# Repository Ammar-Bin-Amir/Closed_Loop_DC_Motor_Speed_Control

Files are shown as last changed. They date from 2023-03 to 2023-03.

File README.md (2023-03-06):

# Closed Loop DC Motor Speed Control

A speed control system's goal is to keep the motor's speed constant under a variety of circumstances. The DC motor is a nonlinear device in practice and speed variations are caused by disturbances, changes in load demand, etc. In this projet, the PID controller algorithm, a common controller in industries, has been implemented which overcome the disturbances occurring in the system and establishes the motor speed to the desired value without any human assistance.

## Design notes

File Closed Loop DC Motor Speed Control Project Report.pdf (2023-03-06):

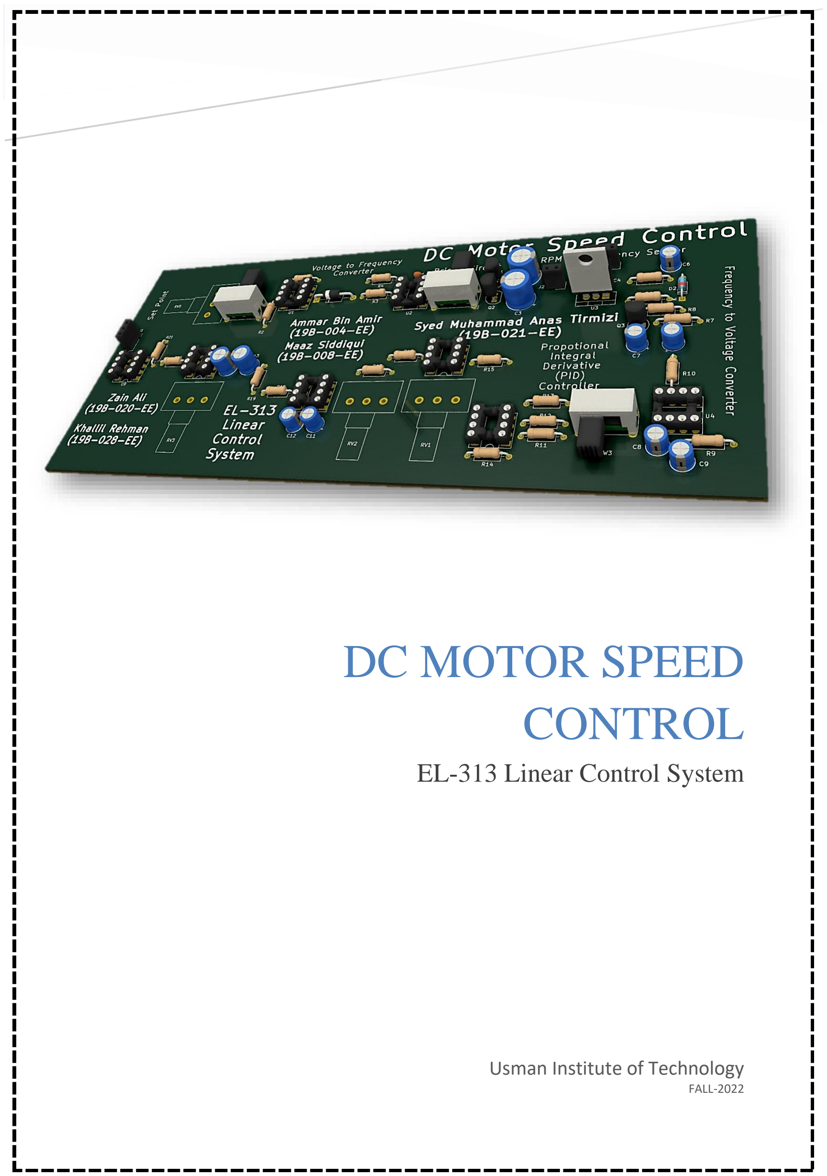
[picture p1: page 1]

# DC MOTOR SPEED CONTROL

## EL-313 Linear Control System

### Usman Institute of Technology

FALL-2022

### Table of Contents

I. Abstract | 2
II. Introduction | 2
III. Literature Review | 3
A. DC Motor Specifications | 3
i. Field Control | 3
ii. Armature Control | 3
B. PID Controller | 3
IV. Proposed System Description | 4
V. Important Observations | 4
VI. | Schematic | 5
VII. | Simulation | 5
VIII. | Hardware | 7
IX. | Tentative Output | 8
X. Problem Faced and Solution | 9
I. Testing Results | 9
II. Conclusion and Future Work | 9
III. References | 9

Table of Tables
Table 1: Parameters of PID Controller | 4

Table of Figures
Figure 1: Block Diagram of DC Motor Speed Control | 2
Figure 2: Block Diagram of PID Controller | 3
Figure 3: Schematic of DC Motor Speed Control | 5
Figure 4: Circuit of PID Controller | 5
Figure 5: Waveforms of PID Controller | 6
Figure 6: Circuit of Voltage to Frequency Converter | 6
Figure 7: Waveforms of Voltage to Frequency Converter | 6
Figure 8: Circuit of Frequency to Voltage Converter | 6
Figure 9: Waveforms of Frequency to Voltage Converter | 6
Figure 10: Circuit of DC Motor Speed Control | 7
Figure 11: Waveforms of DC Motor Speed Control | 7
Figure 12: 2D Layout of PCB | 8
Figure 13: Front 3D Layout of DC Motor Speed Control | 8
Figure 14: Back 3D Layout of DC Motor Speed Control | 8
Figure 15: Front Silk Screen Layer of PCB | 8

I. Abstract

The function of speed control in DC motors is very essential in the achievement of desirable outputs. DC motors are designed for use in industrial and commercial applications. Proportional-Integral-Derivative (PID) controller are considered for controlling the speed of dc motor by giving the step input signal. The response of the motor is investigated using a first order system model of the motor.

An implementation of the controller utilizing OP-AMPs is provided, along with an explanation of the speed control using PID control modes. Designers examine how the controller reacts to changes in load. The system is simulated using KICAD/SIMULINK software. The system responses under PID controllers are also analyzed and discussed in term of their performances.

II. Introduction

It was mainly about P, P-I, P-D and P-I-D controllers, their digital versus continuous time realizations and their characteristics including sampling period effects on the response of digital ones.

A speed control system's goal is to keep the motor's speed constant under a variety of circumstances. The DC motor is a nonlinear device in practice, and speed variations are caused by disturbances, changes in load demand, etc.

The PID controller algorithm, a common controller in industries, has been implemented. The block diagram of a DC motor speed control system. The motor speed is sensed by an optical switch and converted to feedback voltage. It is compared with the reference signal (i.e., desired speed) by the error detector. The PID controller acts on the error signal and generates appropriate control voltage. The PWM generator block than varies the duty cycle of the voltage supplied to the motor to control its speed.

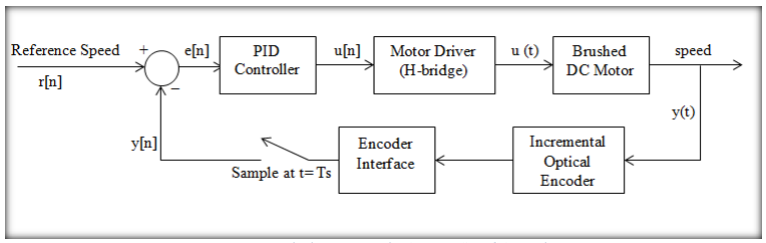
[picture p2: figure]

Figure 1: Block Diagram of DC Motor Speed Control

III. Literature Review

For the implementation of the DC motor speed control system, the concepts of motor and PID controller should be understood.

A. DC Motor Specifications

The speed control system was implemented for a Permanent Magnet DC Motor (PMDC). The PMDC consists of rotor or armature and a stator, which is a permanent magnet. There are two ways of speed control for a DC motor.

i. Field Control

In this method, the field current or current through stator is varied to control the speed of the motor.

ii. Armature Control

In this method, the armature voltage is varied to control the speed of the motor.

For the PMDC, a constant field is generated by a permanent magnet and hence we decided to implement Armature control. To control the armature voltage, we are generating a Pulse-Width Modulated (PWM) waveform to control the average voltage applied to the motor.

B. PID Controller

The combination of proportional, integral and derivative control action is called PID control action. PID controllers are commonly used to regulate the time-domain behavior of many different types of dynamic plants. These controllers are extremely popular because they can usually provide good closed-loop response characteristics.

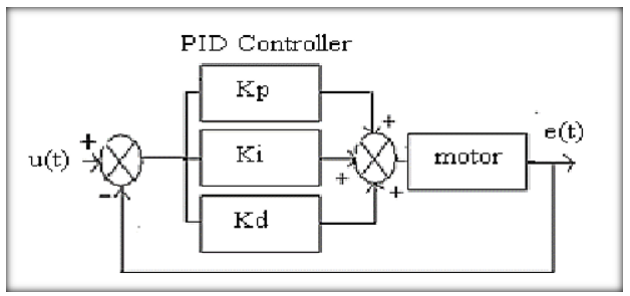
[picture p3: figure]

Figure 2: Block Diagram of PID Controller

Table 1: Parameters of PID Controller

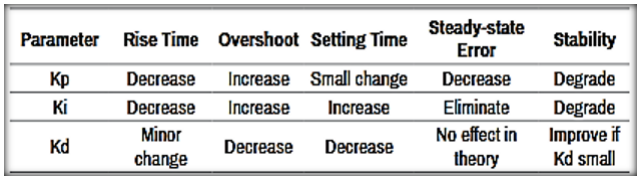
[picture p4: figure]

IV. Proposed System Description

The actual speed of the motor is sensed by the feedback control loop and compares this speed with the preset reference speed in order to determine the required motor’s reference armature current. The simulation of proposed system model has been accomplished.

The PID controller is very popular and common in process control industry. In the PID (proportional-integral-derivative) closed control loop controller, the three controllers P, I and D all have different tuning adjustments which interact all together that’s why its tuning is time consuming and challenging task. The effects of all three individual controllers (P-I-D) summed together to produce the output value of the system. Tuning of PID controller is the major task of this device in order to proper functioning of the PID controller under the given circumstance of the control system.

The variable stand for the error signal used to track the reference signal. The variable is the difference between the desired reference input set point value and the actual output. This error signal is sent to the PID controller and then controller evaluates the derivative and the integral of the error signal. The output signal of the controller becomes equal to the proportional gain (KP) times the magnitude of the error plus the integral gain (KI) times the integral of the error plus the derivative gain (KD) times the derivative of the error.

V. Important Observations

Accurate performance of a motor is desired feature for any industrial application. As the age of motor increases its performance also deceases with aging, so it is desired to evaluate the performance of motor from time to time for efficient operation The conventional method for calculating output performance indices is quite time consuming.

The PID based approach algorithm worked satisfactory for the test system. Following are the observations:

1) The solution time for proposed PID approach is only a fraction of time taken by
| conventional algorithm.
2) A proportional controller Kp will have the effect of reducing the rise time and reduce
| but never eliminate the steady state error.
3) An internal controller Ki will have the effect of eliminate the steady state error, but it
| may make the transient response worse.

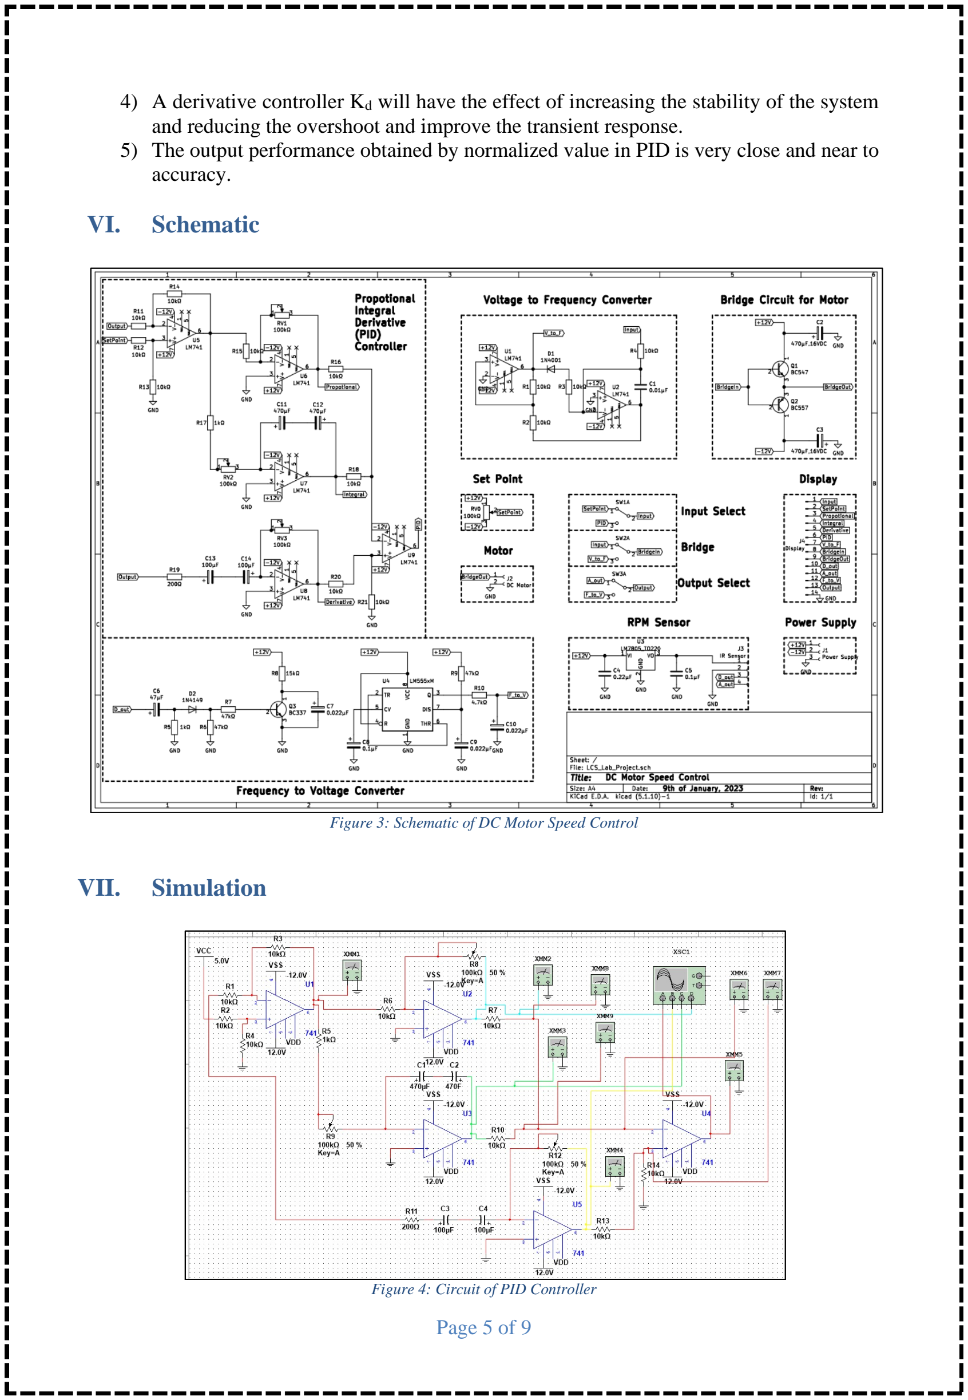
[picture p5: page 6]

4) A derivative controller Kd will have the effect of increasing the stability of the system and reducing the overshoot and improve the transient response.
5) The output performance obtained by normalized value in PID is very close and near to accuracy.

VI. Schematic

Figure 3: Schematic of DC Motor Speed Control

VII. Simulation

Figure 4: Circuit of PID Controller

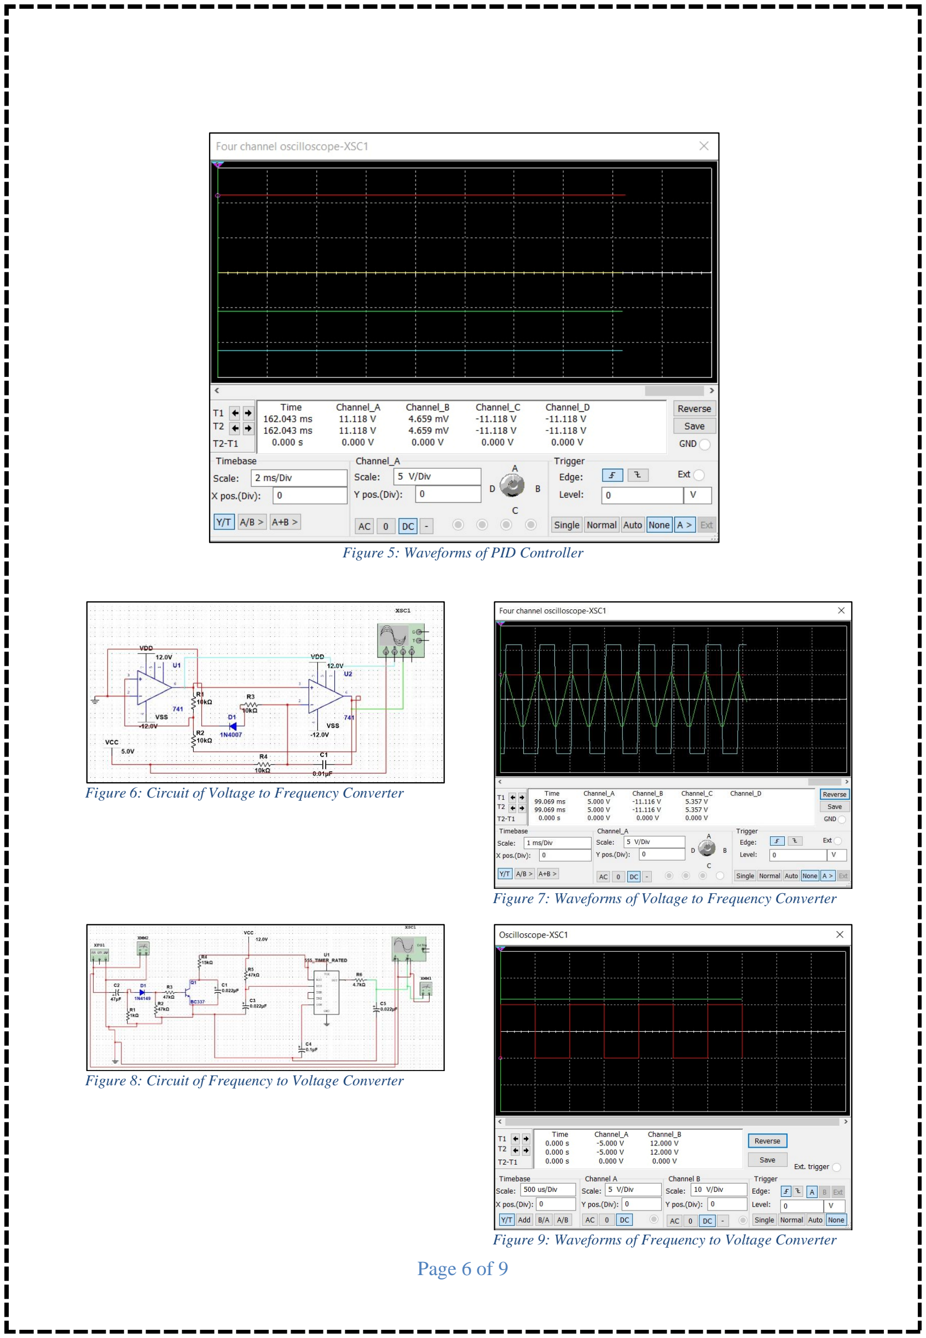
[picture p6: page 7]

Figure 5: Waveforms of PID Controller

Figure 6: Circuit of Voltage to Frequency Converter

Figure 7: Waveforms of Voltage to Frequency Converter

Figure 8: Circuit of Frequency to Voltage Converter

Figure 9: Waveforms of Frequency to Voltage Converter

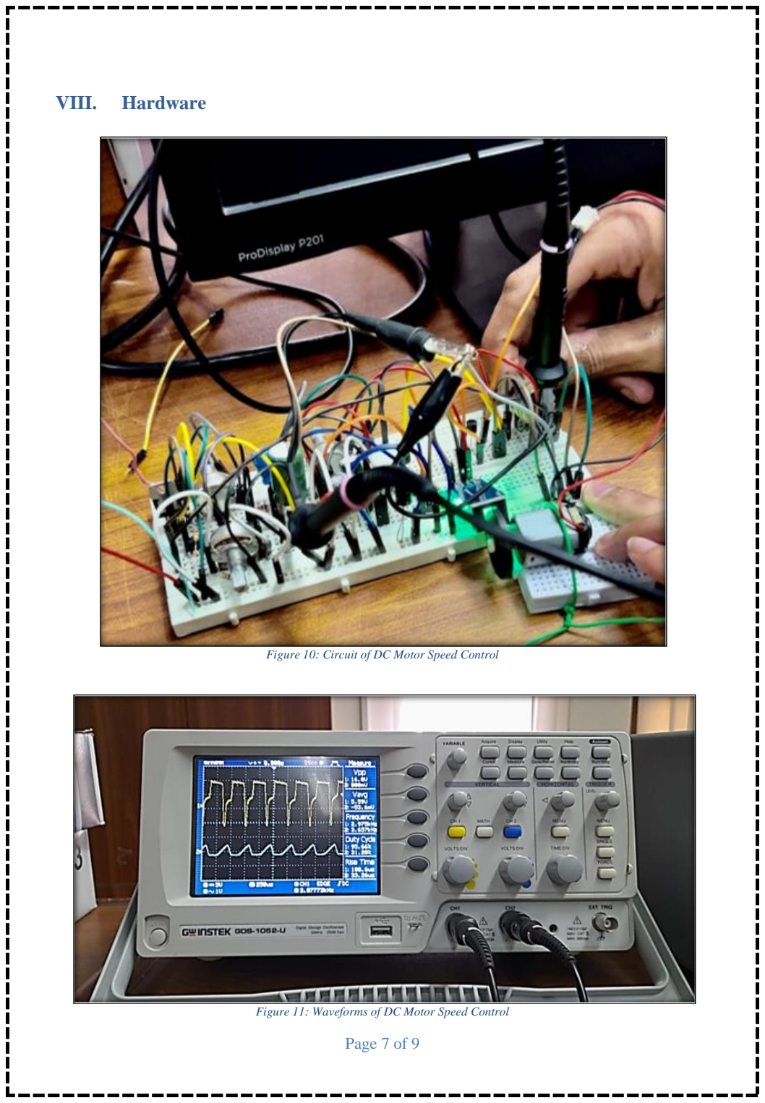
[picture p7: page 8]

VIII. Hardware

Figure 10: Circuit of DC Motor Speed Control

Figure 11: Waveforms of DC Motor Speed Control

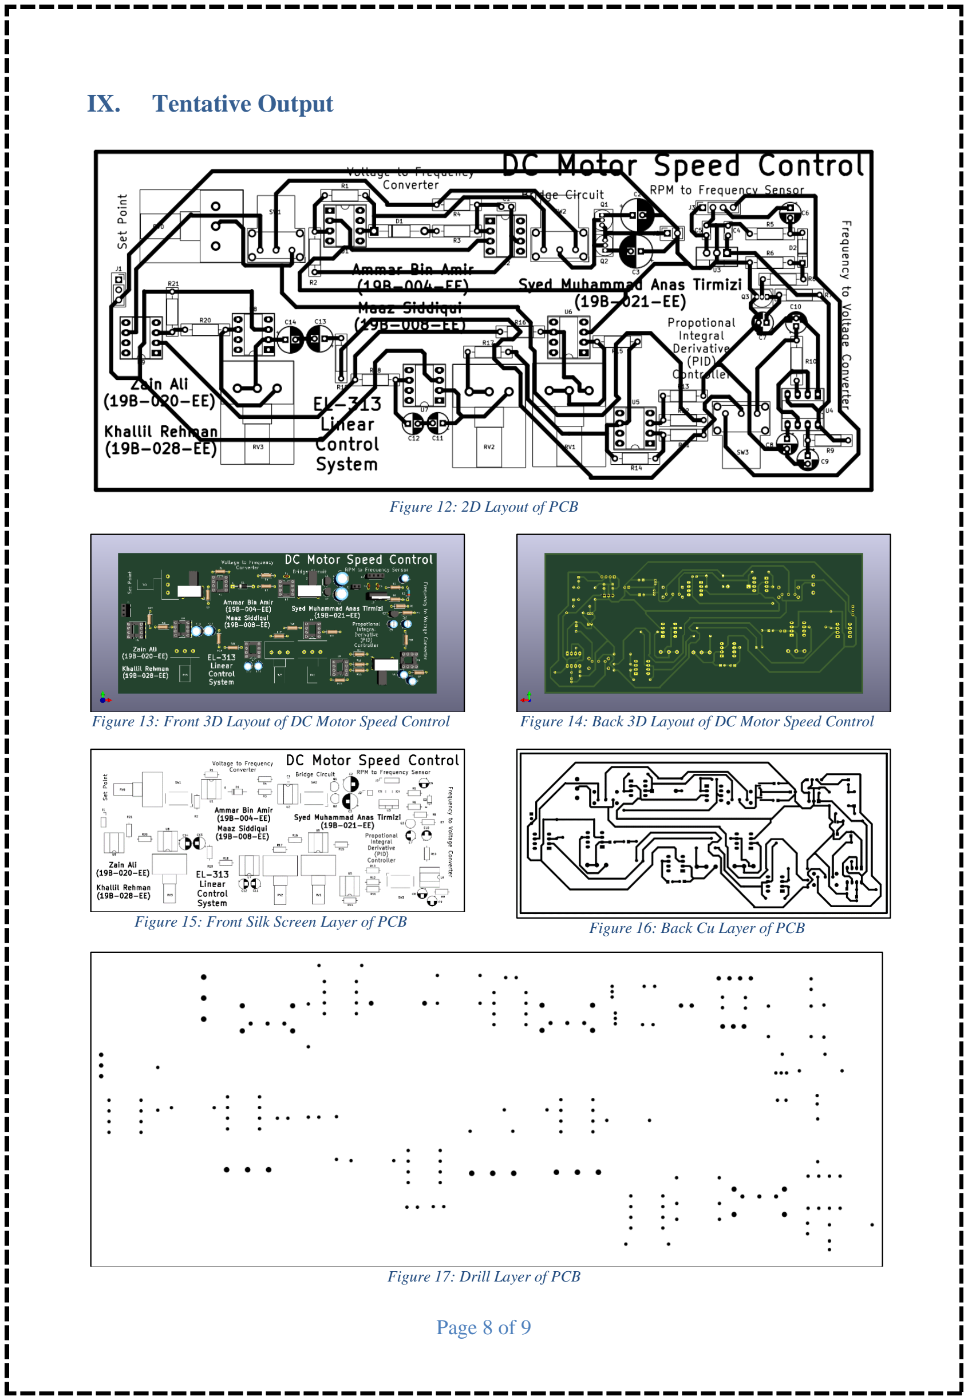
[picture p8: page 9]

IX. Tentative Output

Figure 12: 2D Layout of PCB

Figure 13: Front 3D Layout of DC Motor Speed Control | Figure 14: Back 3D Layout of DC Motor Speed Control
Figure 15: Front Silk Screen Layer of PCB | Figure 16: Back Cu Layer of PCB

Figure 17: Drill Layer of PCB

X. Problem Faced and Solution

To reduce this offset, we modified the circuit to bring back the triangular wave output to the zero reference level. The modified circuit schematic. The circuit uses the feedback mechanism with the comparator (LM 339) and integrator circuit to correct the DC offset error and brings back the triangular wave output to zero reference level. Because of this error correction we are able to generate the PWM pulses from 0% to 100% duty cycle after comparing this triangular wave with the controlled output from PID controller.

I. Testing Results

The DC motor control system was tested with PI and PID controllers. The output waveforms of the PWM generator for two different reference voltage (corresponding to desired speed) and under full load and no-load condition are shown in this section. The DC motor is loaded by magnetic breaking to study the controller performance under load conditions.

II. Conclusion and Future Work

P-I-D control and its variations are commonly used in the industry. They have so many applications. Control engineers usually prefer P-I controllers to control first order plants. On the other hand, P-I-D control is vastly used to control two or higher order plants. In almost all cases fast transient response and zero steady state error is desired for a closed loop system.

However, some improvements can be made in the control aspects of the proposed system design. In this experiment, the PID controller is well performed for the motor speed control under the loaded condition while the speed is kept constant. The ultimate parameter values of PID controller were setup by Manual Tuning method. An Adaptive approach of PID controller may be used in the prospective development in order of effectively speed control of the motor with reference to input speed under the effect of load.

III. References

https://www.elprocus.com/the-working-of-a-pid-controllerhttps://ctms.engin.umich.edu/CTMS/index.php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

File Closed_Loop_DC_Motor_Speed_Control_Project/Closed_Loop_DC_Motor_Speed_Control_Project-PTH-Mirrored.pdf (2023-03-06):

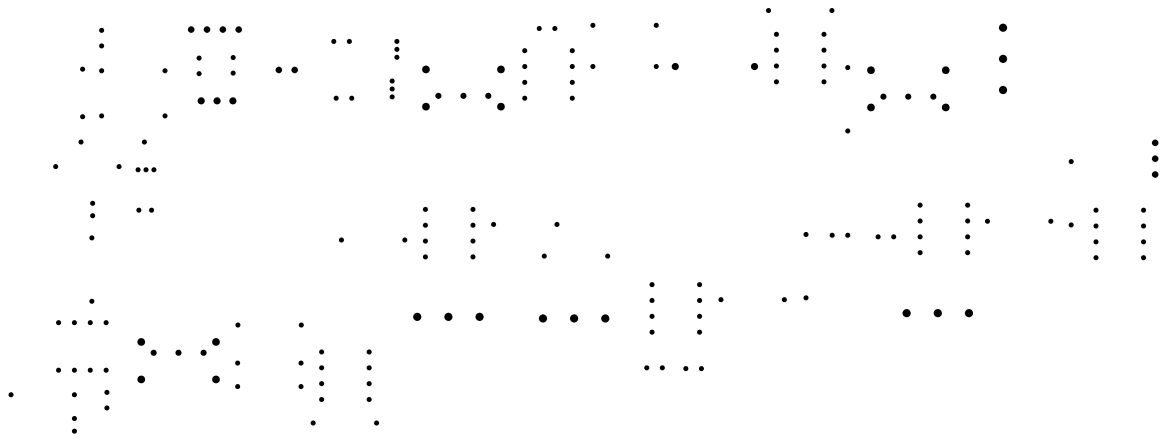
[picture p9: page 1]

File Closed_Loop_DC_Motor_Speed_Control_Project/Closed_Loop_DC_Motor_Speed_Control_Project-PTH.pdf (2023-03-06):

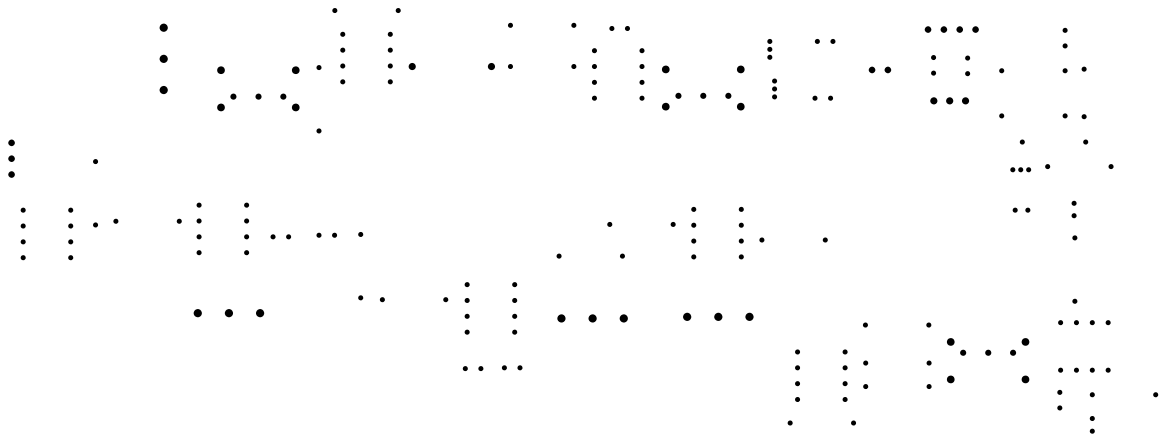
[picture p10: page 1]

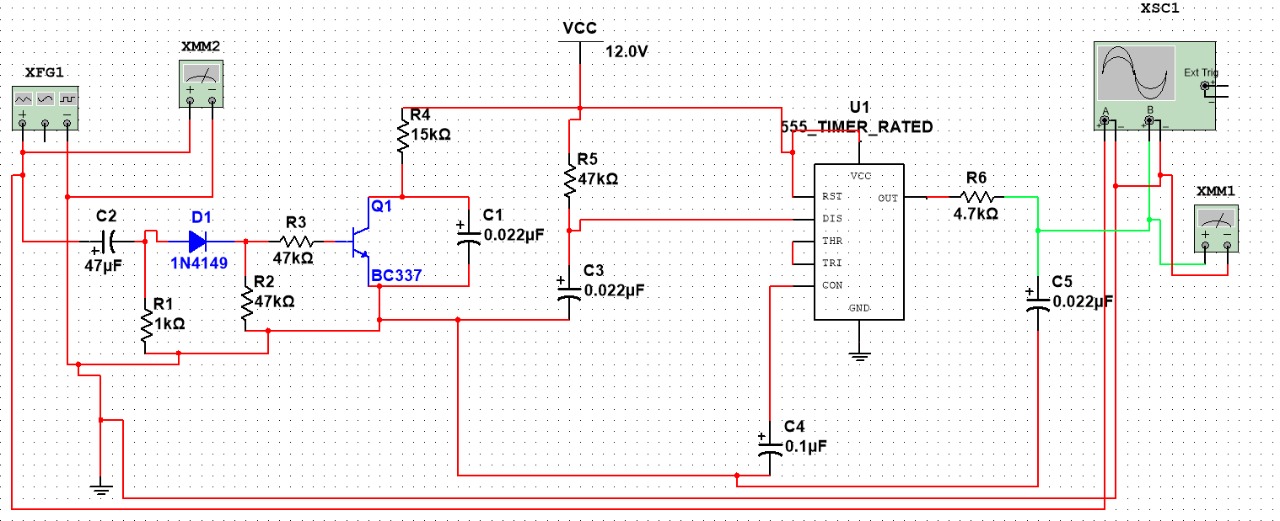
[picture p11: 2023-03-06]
Frequency to Voltage Converter Schematic.jpeg

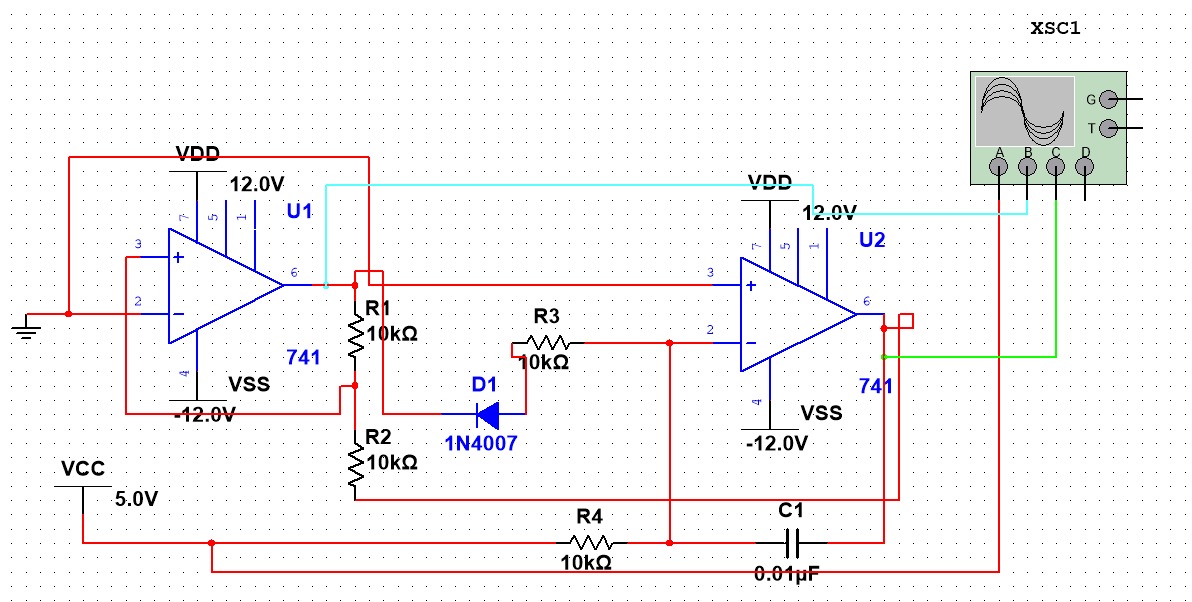
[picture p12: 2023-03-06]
Voltage to Frequency Converter Schematic.jpeg

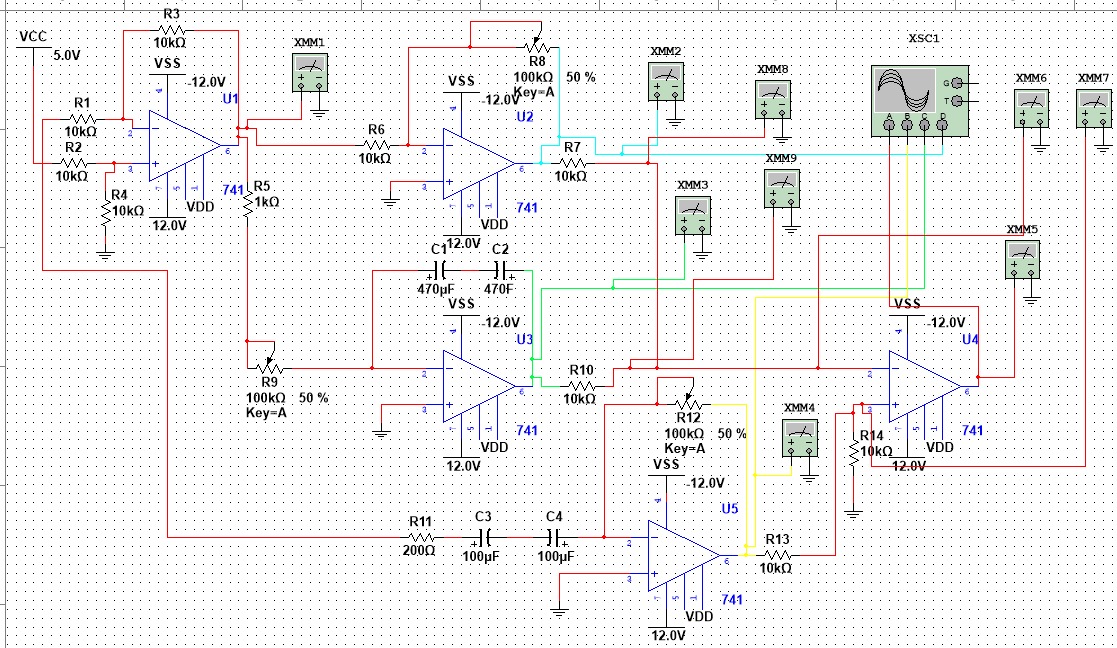
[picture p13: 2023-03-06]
PID Controller Schematic.jpeg

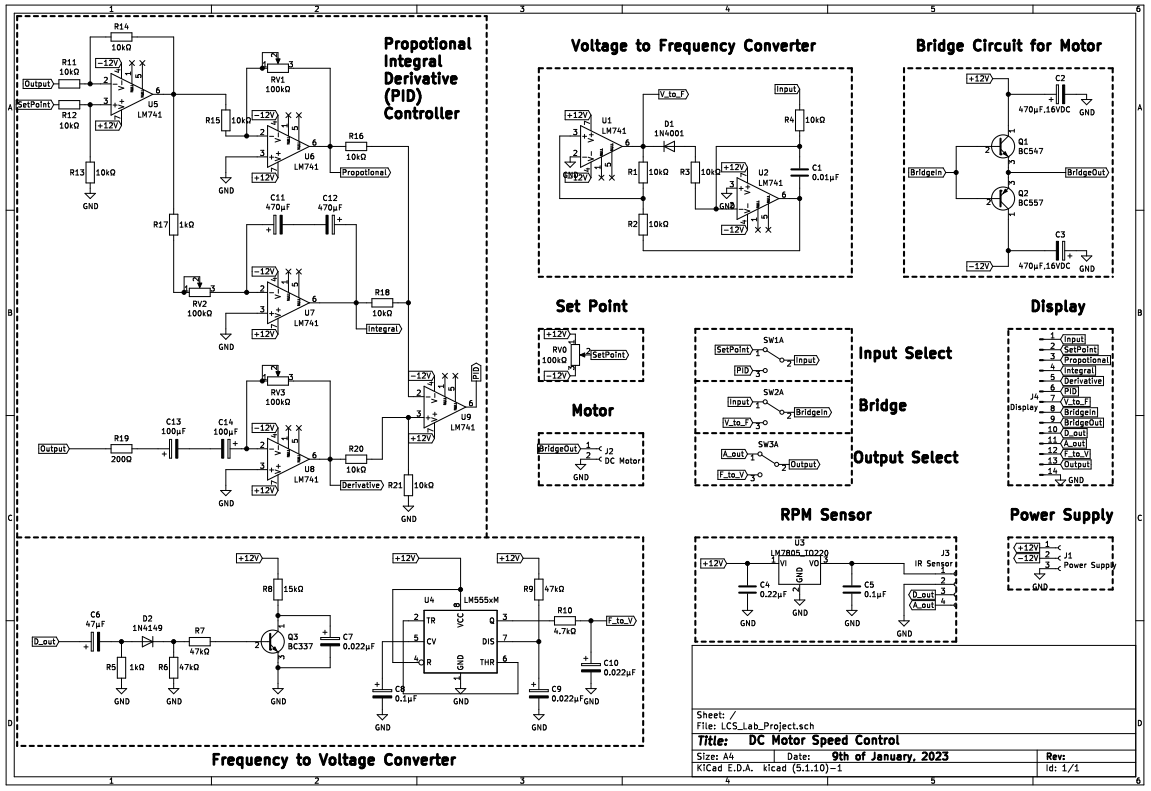
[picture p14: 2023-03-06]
Closed_Loop_DC_Motor_Speed_Control_Project/Closed_Loop_DC_Motor_Speed_Control_Project_Schematic.PNG

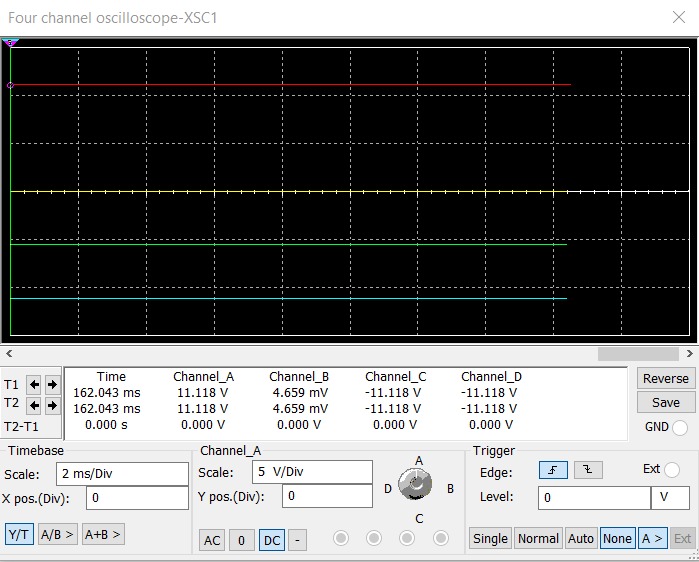
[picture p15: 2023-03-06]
PID Controller Simulation.jpeg

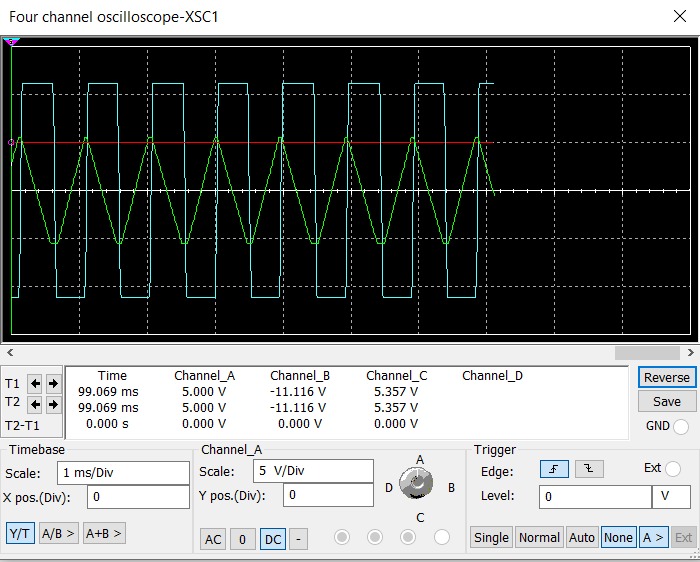
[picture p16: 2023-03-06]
Voltage to Frequency Converter Simulation.jpeg

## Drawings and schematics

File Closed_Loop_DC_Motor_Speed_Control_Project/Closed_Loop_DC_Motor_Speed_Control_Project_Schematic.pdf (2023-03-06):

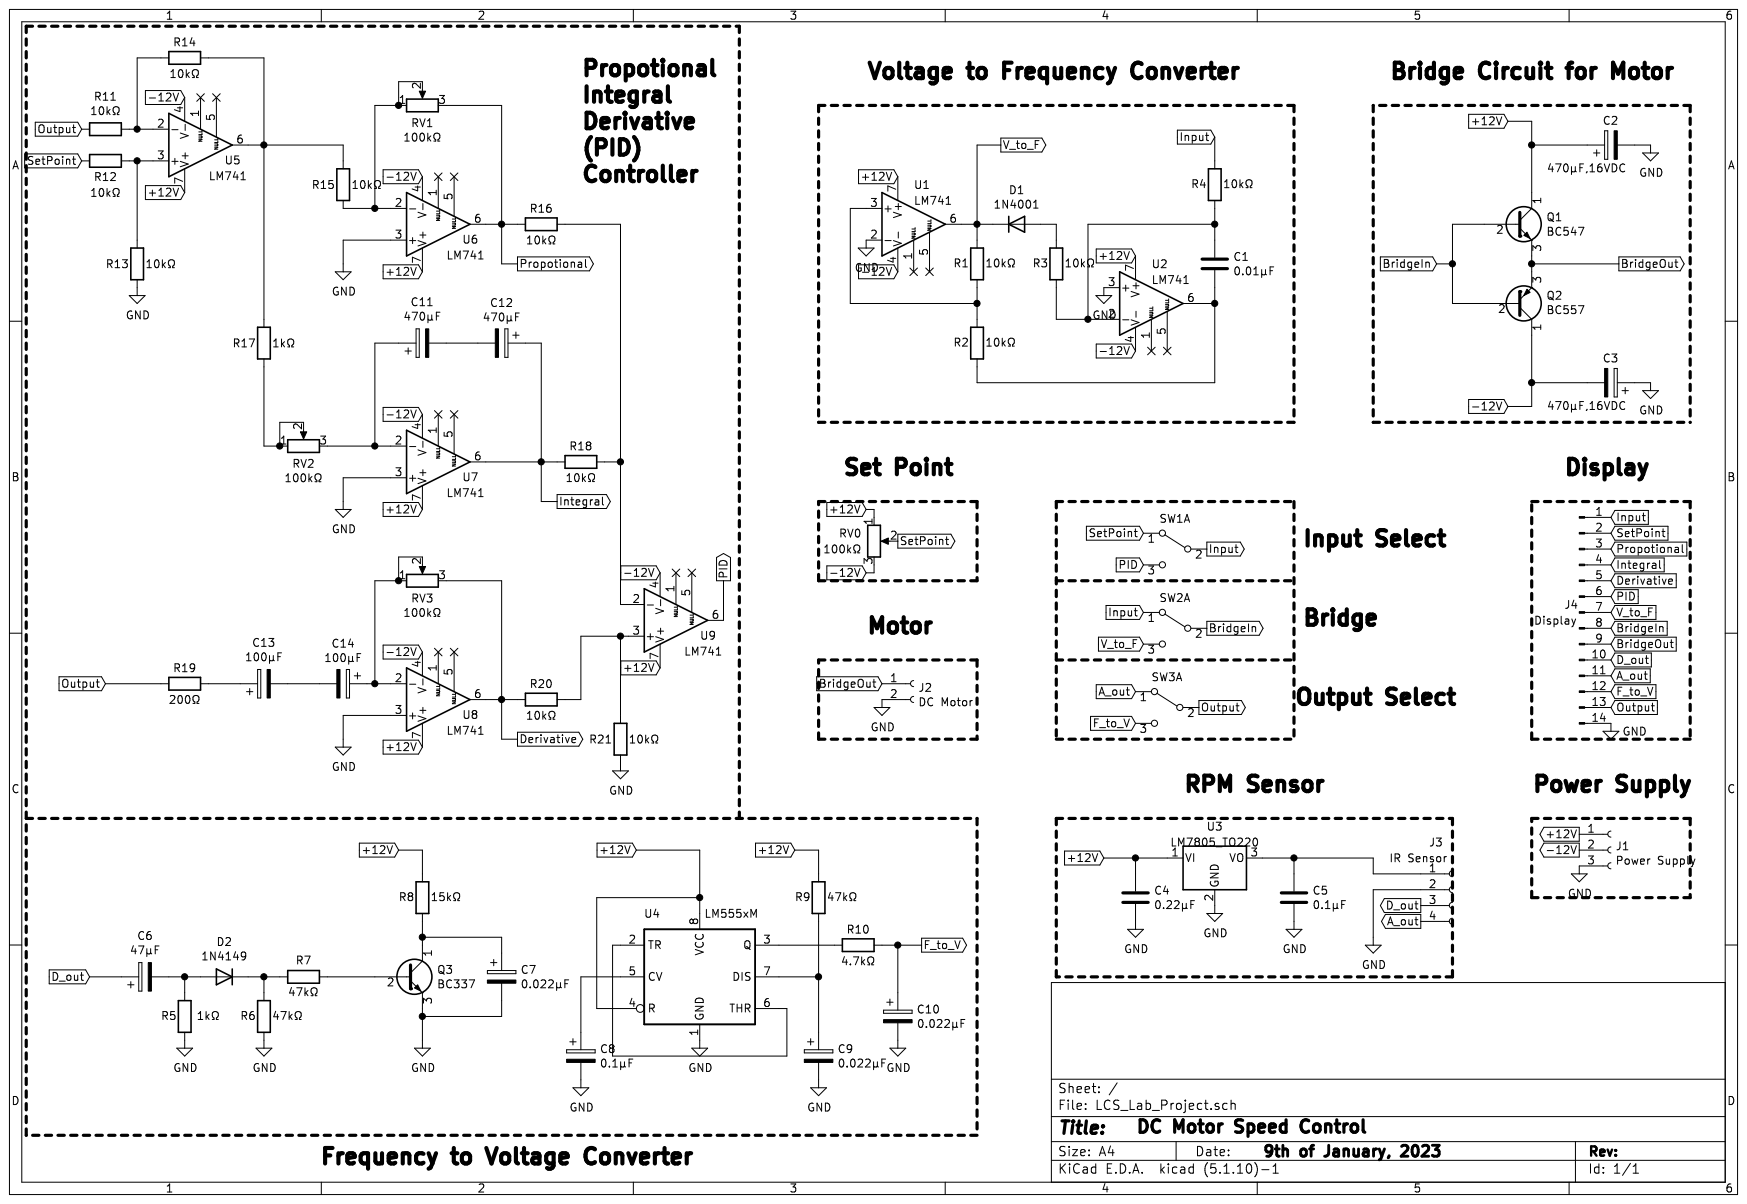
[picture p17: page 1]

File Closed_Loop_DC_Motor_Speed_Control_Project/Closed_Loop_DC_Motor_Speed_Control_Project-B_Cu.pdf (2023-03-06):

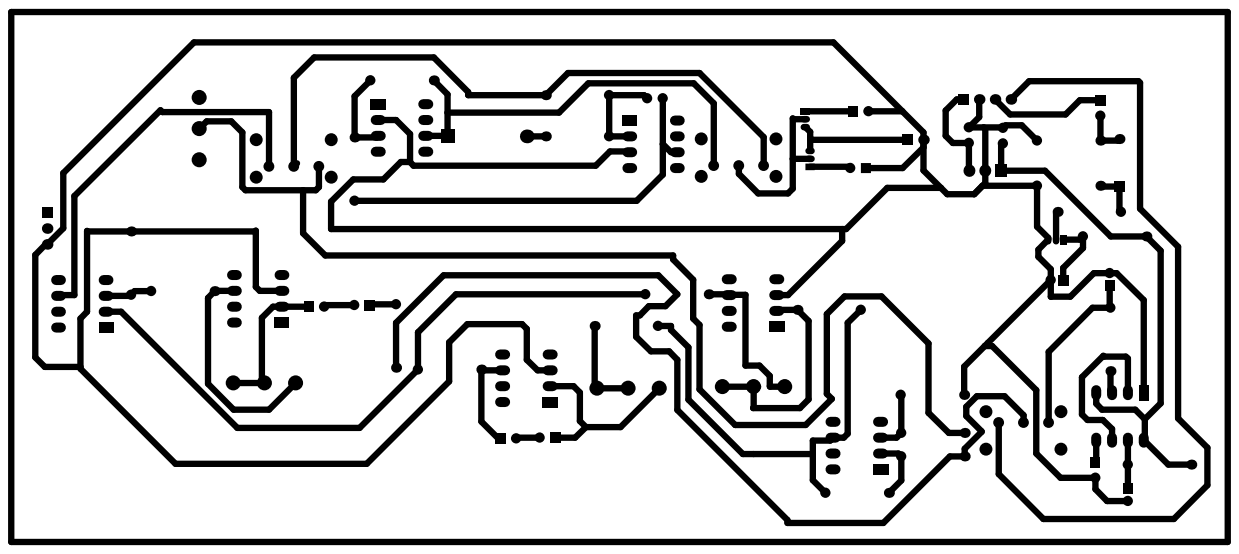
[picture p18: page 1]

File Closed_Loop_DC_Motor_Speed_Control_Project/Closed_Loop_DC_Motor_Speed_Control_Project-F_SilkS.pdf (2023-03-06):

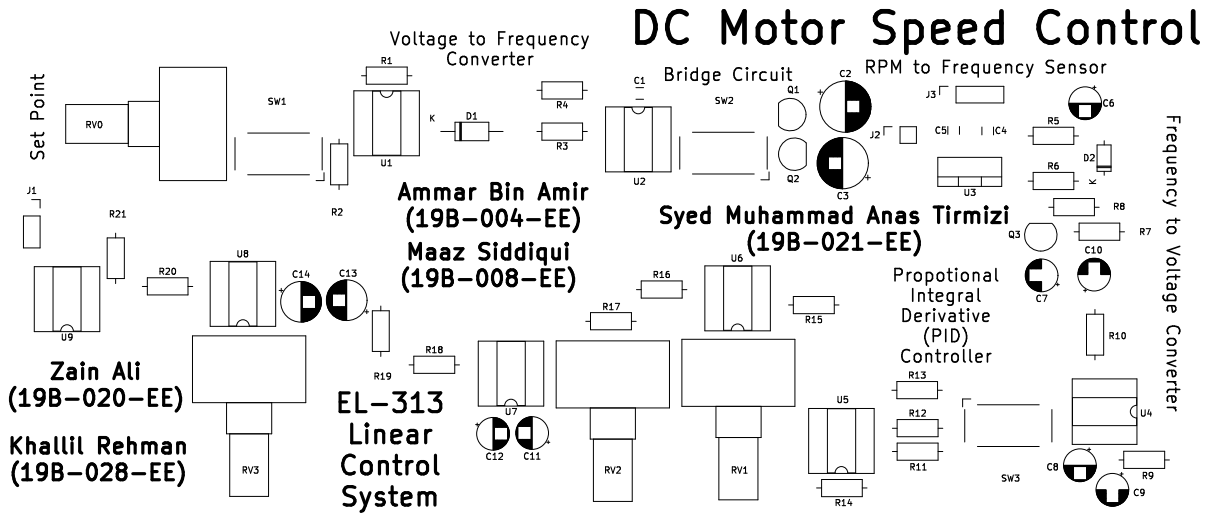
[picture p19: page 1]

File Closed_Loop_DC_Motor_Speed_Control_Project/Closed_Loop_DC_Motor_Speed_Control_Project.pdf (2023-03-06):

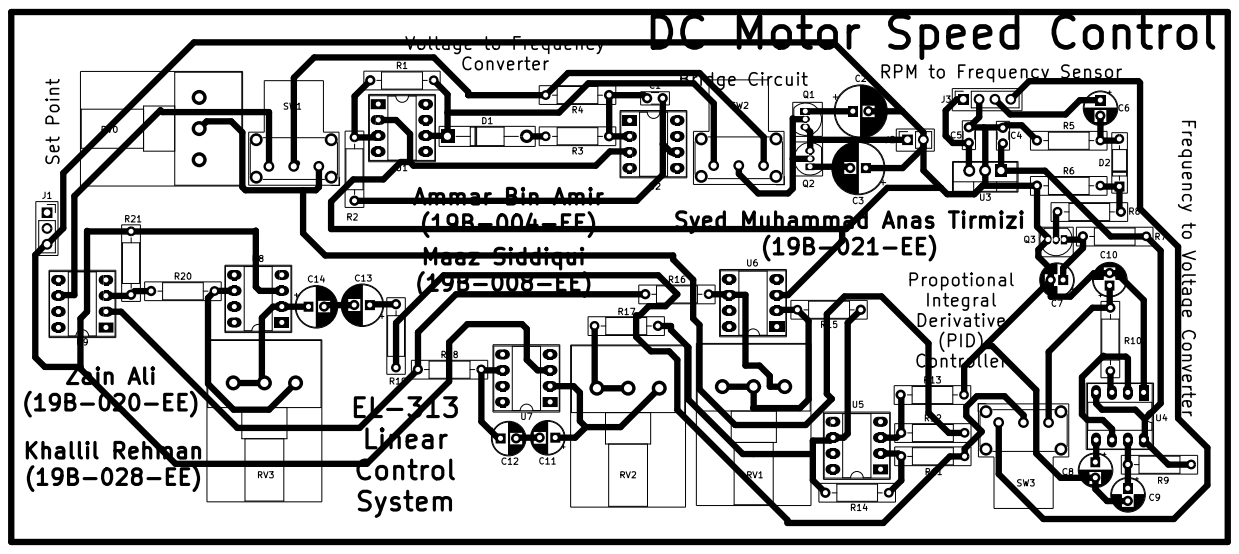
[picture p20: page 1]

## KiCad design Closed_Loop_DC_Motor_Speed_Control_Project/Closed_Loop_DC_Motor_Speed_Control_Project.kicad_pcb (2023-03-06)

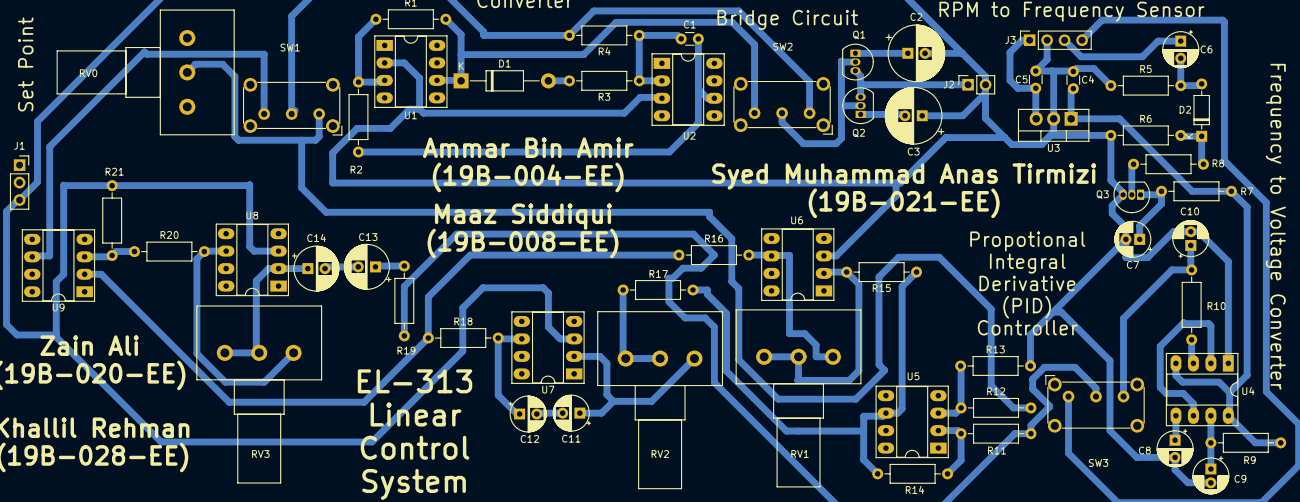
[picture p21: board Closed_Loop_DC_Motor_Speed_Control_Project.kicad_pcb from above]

Board: 2 copper layers, 59 parts (0 on the bottom side), 41 nets.

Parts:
C1: 0.01μF; C_Disc_D3.0mm_W1.6mm_P2.50mm
C2, C3: 470μF,16VDC; CP_Radial_D8.0mm_P2.50mm
C4: 0.22μF; C_Disc_D3.0mm_W1.6mm_P2.50mm
C5: 0.1μF; C_Disc_D3.0mm_W1.6mm_P2.50mm
C6: 47μF; CP_Radial_D5.0mm_P2.50mm
C7, C9, C10: 0.022μF; CP_Radial_D5.0mm_P2.00mm
C8: 0.1μF; CP_Radial_D5.0mm_P2.50mm
C11, C12: 470μF; CP_Radial_D5.0mm_P2.50mm
C13, C14: 100μF; CP_Radial_D6.3mm_P2.50mm
D1: 1N4001; D_DO-41_SOD81_P12.70mm_Horizontal
D2: 1N4149; D_DO-35_SOD27_P7.62mm_Horizontal
J1: Power Supply; PinSocket_1x03_P2.54mm_Vertical
J2: DC Motor; PinSocket_1x02_P2.54mm_Vertical
J3: IR Sensor; PinSocket_1x04_P2.54mm_Vertical
Q1: BC547; TO-92_Inline
Q2: BC557; TO-92_Inline
Q3: BC337; TO-92_Inline
R1, R2, R3, R4, R11, R12, R13, R14, R15, R16, R18, R20, R21: 10kΩ; R_Axial_DIN0207_L6.3mm_D2.5mm_P10.16mm_Horizontal
R5, R17: 1kΩ; R_Axial_DIN0207_L6.3mm_D2.5mm_P10.16mm_Horizontal
R6, R7, R9: 47kΩ; R_Axial_DIN0207_L6.3mm_D2.5mm_P10.16mm_Horizontal
R8: 15kΩ; R_Axial_DIN0207_L6.3mm_D2.5mm_P10.16mm_Horizontal
R10: 4.7kΩ; R_Axial_DIN0207_L6.3mm_D2.5mm_P10.16mm_Horizontal
R19: 200Ω; R_Axial_DIN0207_L6.3mm_D2.5mm_P10.16mm_Horizontal
RV0, RV1, RV2, RV3: 100kΩ; Potentiometer_Alps_RK163_Single_Horizontal
SW1, SW2, SW3: SW_DPDT_x2; SW_E-Switch_EG1224_SPDT_Angled
U1, U2, U5, U6, U7, U8, U9: LM741; DIP-8_W7.62mm_Socket_LongPads
U3: LM7805_TO220; TO-220-3_Vertical
U4: LM555xM; DIP-8_W7.62mm_Socket_LongPads

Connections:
+12V: C2.1, C4.1, J1.1, Q1.1, R8.2, R9.2, RV0.1, U1.7, U2.7, U3.1, U4.4, U4.8, U5.7, U6.7, U7.7, U8.7, U9.7
-12V: C3.2, J1.2, Q2.1, RV0.3, U1.4, U2.4, U5.4, U6.4, U7.4, U8.4, U9.4
A_out: J3.4, SW3.1
BridgeIn: Q1.2, Q2.2, SW2.2
BridgeOut: J2.1, Q1.3, Q2.3
D_out: C6.1, J3.3
Derivative: R20.2, RV3.3, U8.6
F_to_V: C10.1, R10.1, SW3.3
GND: C2.2, C3.1, C4.2, C5.2, C7.2, C8.2, C9.2, C10.2, J1.3, J2.2, J3.2, Q3.3, R5.1, R6.1, R13.2, R21.2, U1.2, U2.3, U3.2, U4.1, U6.3, U7.3, U8.3
Input: R4.2, SW1.2, SW2.1
Integral: C12.1, R18.2, U7.6
unnamed: C1.1, R3.1, R4.1, U2.2
unnamed: C1.2, R2.1, U2.6
unnamed: C5.1, J3.1, U3.3
unnamed: C6.2, D2.2, R5.2
unnamed: C7.1, Q3.1, R8.1
unnamed: C8.1, U4.5
unnamed: C9.1, R9.1, U4.7
unnamed: C11.1, RV2.3, U7.2
unnamed: C11.2, C12.2
unnamed: C13.1, R19.1
unnamed: C13.2, C14.2
unnamed: C14.1, RV3.1, RV3.2, U8.2
unnamed: D1.2, R3.2
unnamed: D2.1, R6.2, R7.1
unnamed: Q3.2, R7.2
unnamed: R1.1, R2.2, U1.3
unnamed: R10.2, U4.3
unnamed: R11.1, R14.2, U5.2
unnamed: R12.1, R13.1, U5.3
unnamed: R14.1, R15.1, R17.1, U5.6
unnamed: R15.2, RV1.1, RV1.2, U6.2
unnamed: R16.1, R18.1, U9.2
unnamed: R17.2, RV2.1, RV2.2
unnamed: R20.1, R21.1, U9.3
unnamed: U4.2, U4.6
Output: R11.2, R19.2, SW3.2
PID: SW1.3, U9.6
Propotional: R16.2, RV1.3, U6.6
SetPoint: R12.2, RV0.2, SW1.1
V_to_F: D1.1, R1.2, SW2.3, U1.6
